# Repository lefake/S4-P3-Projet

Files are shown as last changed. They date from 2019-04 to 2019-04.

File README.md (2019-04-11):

# S4-P3-Projet
PCB maker project



This is a PCB maker device, it is use to create PCB from an image in black and white. Three software are include in this repo : 
  - GCode Generator :
      Create a GCode file form an image of the PCB
  - Device communication :
      Send a GCode file to the device
      Manual control of the device
  - GCode Interpreter :
      Move motors from a GCode command

For more documentation on each software read the README files in every directory.

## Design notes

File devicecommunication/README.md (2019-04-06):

# Device Communication

This code is use to communicate with the device

## Getting Started

To use this UI you must have a GCode file to sent to the device unless you want to control manually the device.

### Prerequisites

Since the program is coded in python, you need to install python, we used python 3.7.
You can use an IDE or cmd to launch the program or the UI.

## Using the program

After downloading the project,
You can launch CommunicationMain.py in S4-P3-Projet/devicecommunication/ for the user interface of the program.

### Automatic mode

Enter the parameters in the proper boxes:

```
- The GCode file's path.
- COM port of the OpenCR (ex: COM8).
- The communication baudrate of the OpenCR.
- Maximum communication time in seconds.
  This is the maximum time to accept an anwser when a command is request.
- Sleep inital time in seconds. 
  This is the boot time of the OpenCR. The time to wait before sending the first command.
```
Once all parameters are entered, you can click on the **Start** button.
At the moment everything runs in one thread so the UI is block by the communication

### Manual mode

The manual mode uses the values entered in the Auto tab so be sure the COM port is specified.
At the moment all +/- buttons dont move the motors in a relative movement. 
Hence it's better to use the text field to move the mototrs

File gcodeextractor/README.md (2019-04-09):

# GCode Extractor

This program transforms a pcb drawing into a gcode.

## Getting started

To use this program, you need to launch main.py with the proper parameters or launch UI.py in /UI/ and enter the parameters in the boxes.
The PCB drawing you are using needs to be of format *.pbm ,
there are plenty of converters online to change your file format, such as [this converter we used](https://convertio.co/fr/pdf-pbm/).

### Prerequisites

Since the program is coded in python, you need to install python, we used python 3.7.
You can use an IDE or cmd to launch the program or the UI.

### Using the program

After downloading the project, you can launch UI.py in S4-P3-Projet/gcodeextractor/UI/ for the user interface of the program.

Enter the parameters in the proper boxes:

```
- Pcb drawing file path you want to convert into gcode, this file needs to be of type *.pbm
- Gcode file you want to save with the path where you want to save it.
  If the file doesn't exist, a new file will be created, file type needs to be *.gcode
- If the pbm file is of type binary or ASCII. To find the type, you can open the file in a text editor,
  ASCII files will start with P1 while binary with P4. Also, binary type will contain unreadable characters.
- Width of your pcb, units are entered later, 
- Height of your pcb, it must be of the same units as the width
- Radius of the tool you are using, units must be in mm.
- Units type for the width and height
```
Once all parameters are entered, you can click on the **execute program** button.
If everything is good, you should read **SUCCESS** on the bottom of the UI, else and error code should appear.

### Algorithms

To convert a pcb image into a gcode, we first find where the tool will have to travel, in order to create the pcb. This is done in the path.py file. The pcb image is a matrix in which the connections are represented by 1's and the empty space by 0's, we use 2's to represent the tool's path. path.py has 3 functions, the first one (scanHorizontal) adds 2's on the left or the right of 1's if they are the beginning or end of a line, it adds a column of 2's the size of the tool's diameter at a tool's radius away from the 1. the second function (scanVertical) is similar but instead of looking and adding on the left or right side, it does on the up or down side. The third function (twoRemoving) removes 2's where there shouldn't be, by looking near the 1's and removing 2's that would make the tool touch the 1.

We then create a sequence of coordinates for the tool to follow to cover all the path we just created. This is done in gcodeCreator.py. We create a sequence of straight lines only, circles or diagonals are a sum of straight lines. The sequence is created by the function *create sequence* that goes through all pixels in the image to find a 2 where the tool will start working. It starts the sequence by a set of coordinates (-1,-1), which means it is starting a new path, and a set of coordinates where the 2 is. Then it uses the function *findDirection* to seek for 2's nearby to find a direction where to travel. It will continue in this direction with the function *findEndOfLine* until it hits the last 2 of the line, adding its coordinates to the sequence, and then seek for another direction until it can't find any 2's. All the 2's covered by the sequence are changed by 3's so the algorithm never cover the same 2 twice. Once it comes to the end of a path, the algorithm will continue looking for 2's where to start paths from until it has looked through all the pixels of the image.

The last file is GcodeBuilder.py, it transforms the sequence of point into a standard gcode file. It does so by changing the coordinates in pixels, into coordinates in mm according to the dimensions of the pcb. If the coordinates are (-1,-1), this means the sequence has finished a path and the tool should not be working until it gets to the next coordinates. The gcode file also starts with a header and ends with a footer to add some configurations and a homing.

### Tests

For path.py's function, we tested the three functions with small matrix of 0's and 1's and wrote the expected results manually to compare if the functions returned what we expected. We also tested if the algorithms would still work if it had to write or read out of bound of the image, which is verified in the algorithms. 

The tests for GcodeCreator.py were made in a similar way, with small matrices of 0's and 2's and an expected sequence of coordinates to compare. We also tested if the algorithm had to read out of bound of the image.

For GcodeBuilder.py, we created some coordinates sequences and a similar but simpler algorithm that would give us the resulting gcode. We compared the function's results with the simpler algorithm's results to see if they were the same. We also tested for different pixel sizes.

## Authors

**Ian Lalonde** 

**Marc-Antoine Lafrenière**

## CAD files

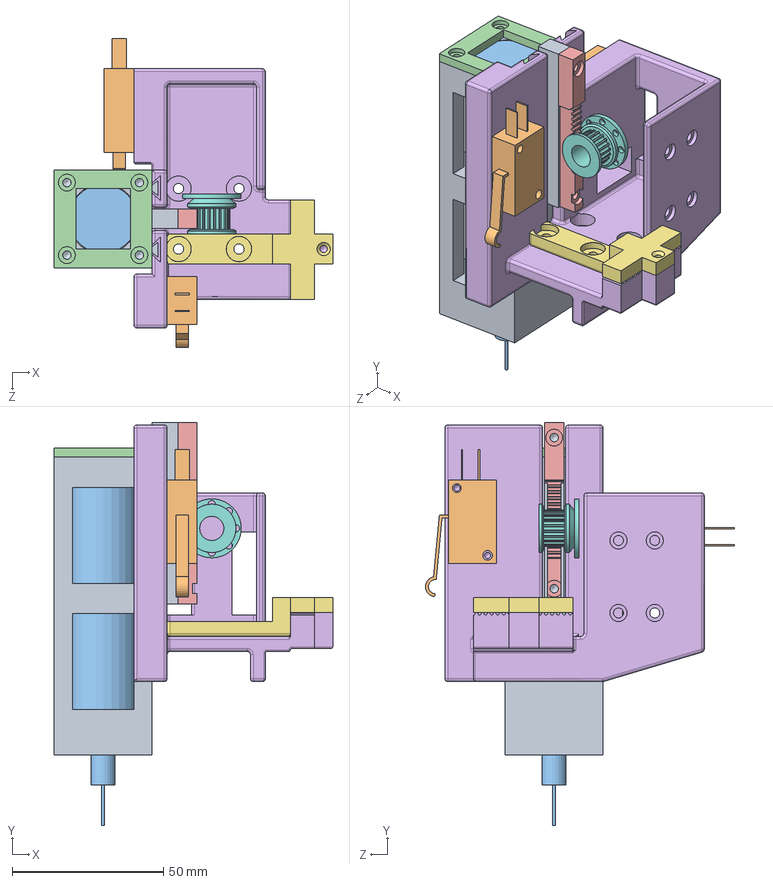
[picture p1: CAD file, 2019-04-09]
Machine PCB/assemblage dremel.SLDASM
92.2 x 133.4 x 102.3 mm
support dremel male
LIMIT SWITCH x 2
modèle dremel
couvercle support
gear
support dremel
Adapteur_MGN14
GT2_20T_Costom2

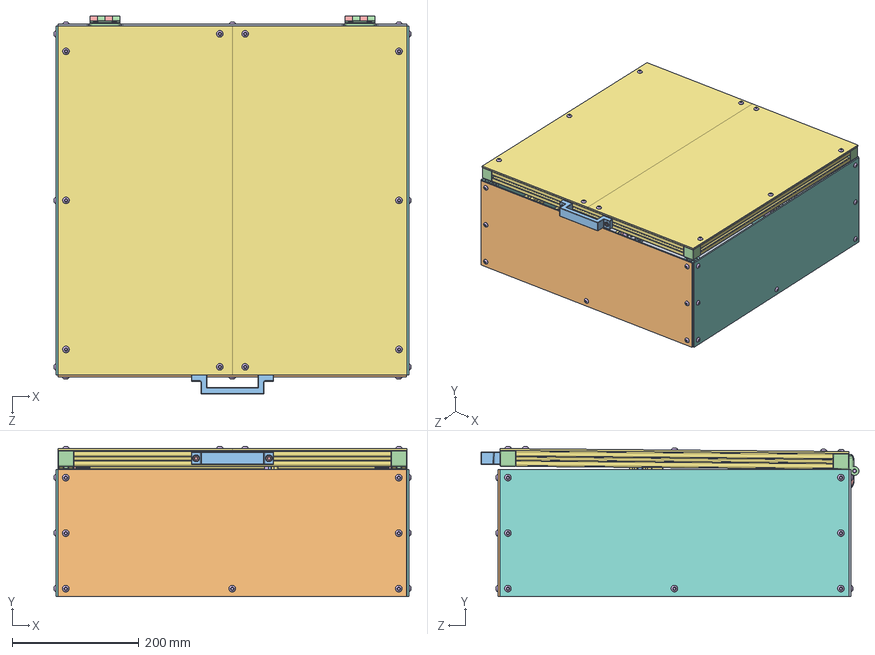
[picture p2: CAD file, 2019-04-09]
Machine PCB/Assemblage.SLDASM
562.6 x 236.6 x 595.9 mm
MGN_12_H_RAIL x 2
MGN_12_H_CARRAGE x 3
MGN_12_H_RAIL_310mm
Adapteur_MGN12 x 2
socket head cap screw_am x 61
94180A351_HEAT-SET INSERTS FOR PLASTICS x 2
25_2525_500mm x 15
14164_m x 22
Adapteur_MGN12_2
Adapteur_MGN12_3
Support_moteur_axe_y_1
634068.step x 3
545412.step x 6
535198.step x 6
socket head cap screw_ai x 12
GT2_20T_Costom
GT2_20T x 3
Adapteur_support_bearing
633104.step x 4
coupleur
Plaque_bearing
Belt_1
Belt_2
Panneau_1 x 2
Panneau_3
Panneau_2
handle
_12099_m_a_2 x 2
_12099_m_b_4 x 2
_12098_m_pin_6 x 2
socket countersunk head screw_am x 8
25_2525_200mm x 4
bed_2
bed_1
moteurgros x 2
coins_couvercle x 4
fer_angle x 5
socket button head cap screw_am x 60
Panneau_4 x 2
X-430_IDLE.stp
X-430_SPACER_RING.stp x 8
X-430_CVR_CABLE.stp
bed corner
bed slider x 2
braquette_1_LS
LIMIT SWITCH x 5
braquette_2_LS
Panneau_5
Panneau_6
braquette_3_LS
support dremel male
modèle dremel
couvercle support
gear
support dremel
Adapteur_MGN14
GT2_20T_Costom2
flat head screw_am
hex screw_am x 3

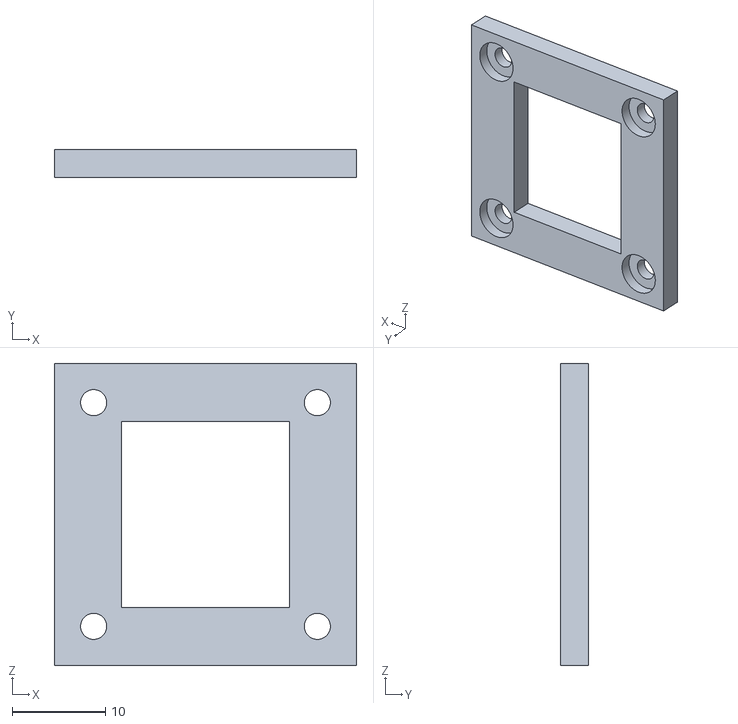
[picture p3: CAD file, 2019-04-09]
Fichiers STL/couvercle support.STL
32.4 x 3.00 x 32.4

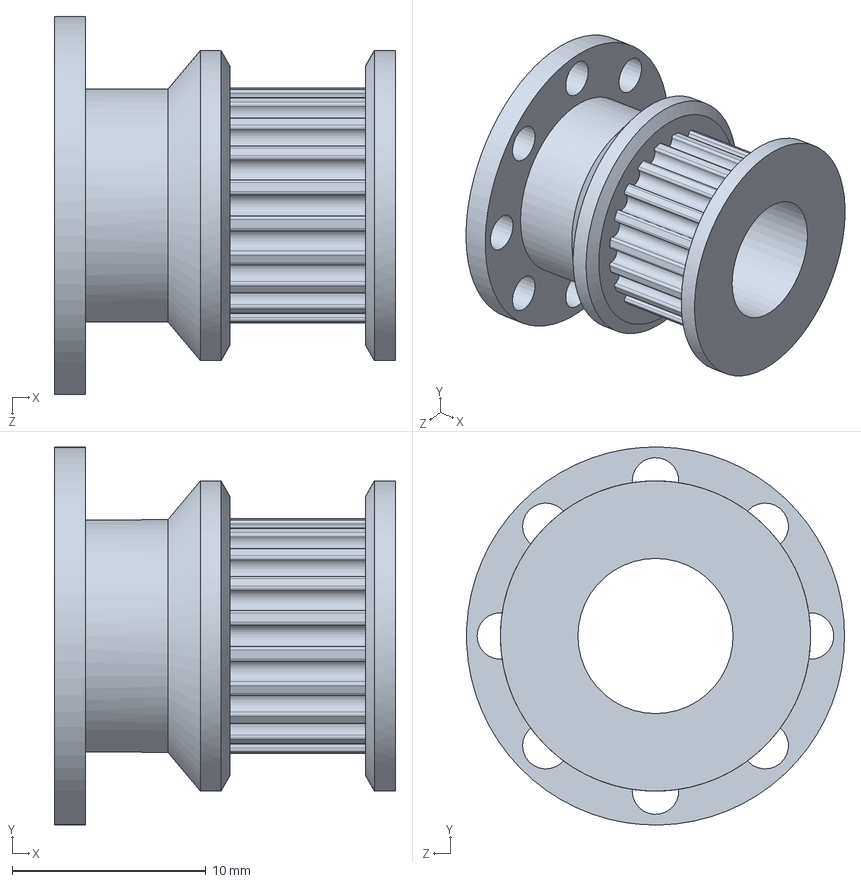
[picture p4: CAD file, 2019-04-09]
Machine PCB/GT2_20T_Costom.SLDPRT
17.6 x 19.5 x 19.5 mm

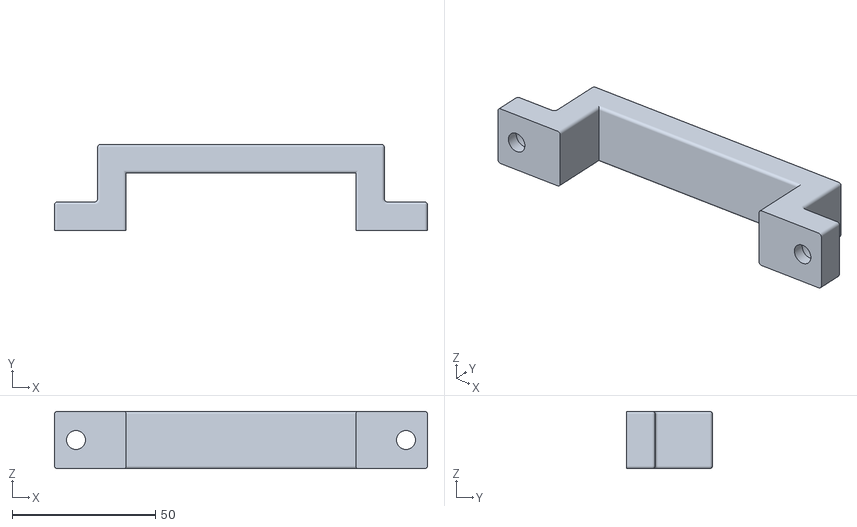
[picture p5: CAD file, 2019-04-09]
Fichiers STL/handle.STL
130.0 x 30.0 x 20.0

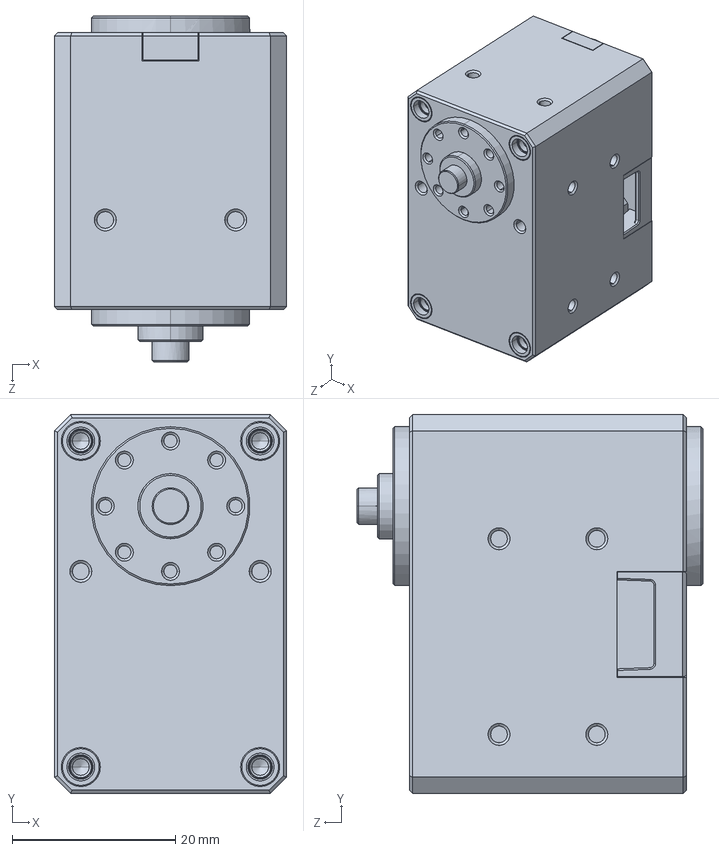
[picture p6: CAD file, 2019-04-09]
Machine PCB/moteurgros.SLDPRT
28.5 x 46.5 x 42.4 mm

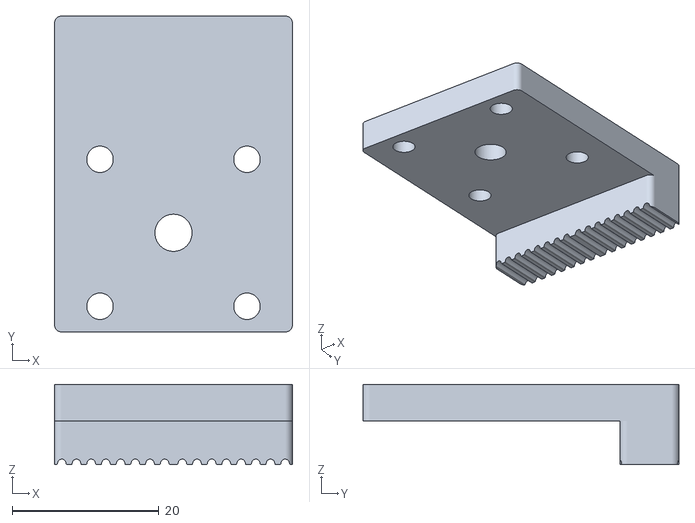
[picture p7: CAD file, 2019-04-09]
Fichiers STL/Adapteur_MGN12.STL
32.4 x 43.0 x 10.9

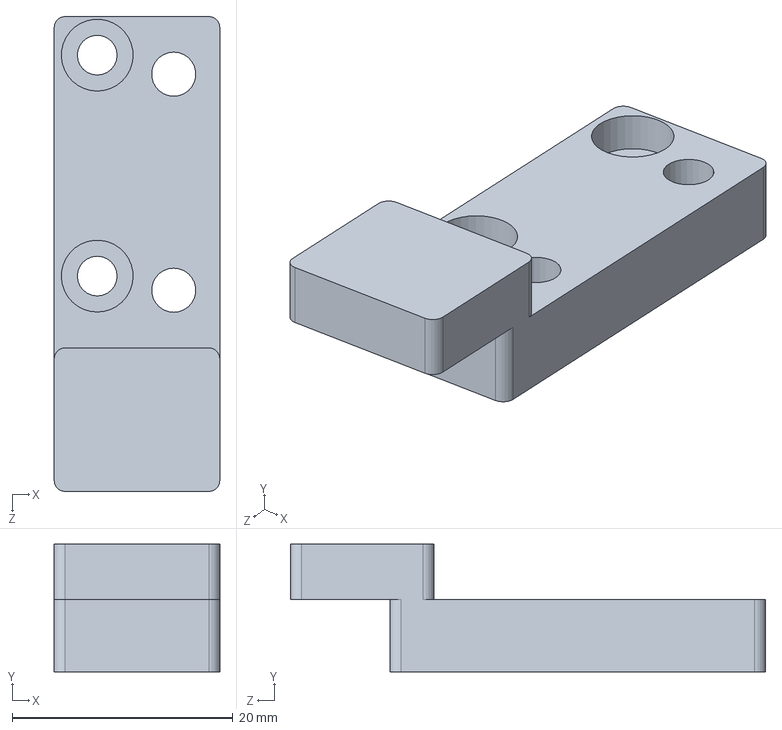
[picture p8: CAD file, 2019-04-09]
Machine PCB/Adapteur_MGN12_2.SLDPRT
15.0 x 11.6 x 43.0 mm

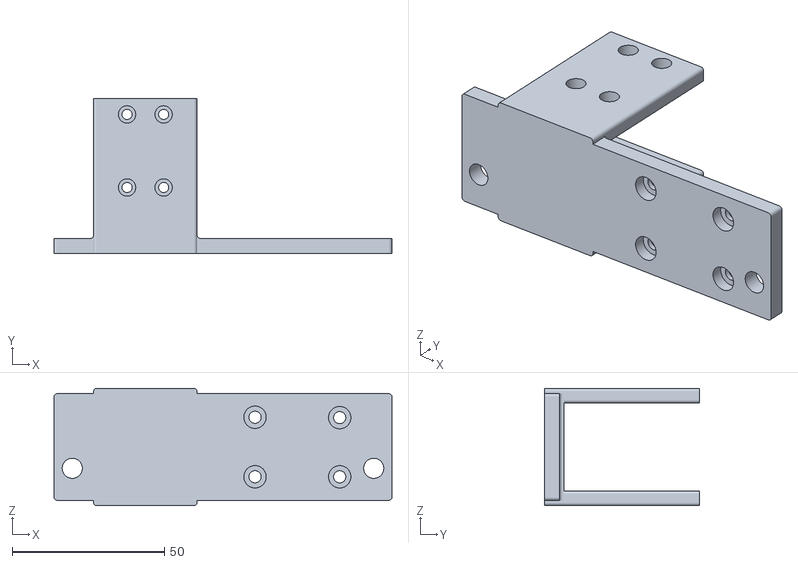
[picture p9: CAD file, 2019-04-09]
Fichiers STL/Adapteur_support_bearing.STL
111.0 x 50.9 x 38.5

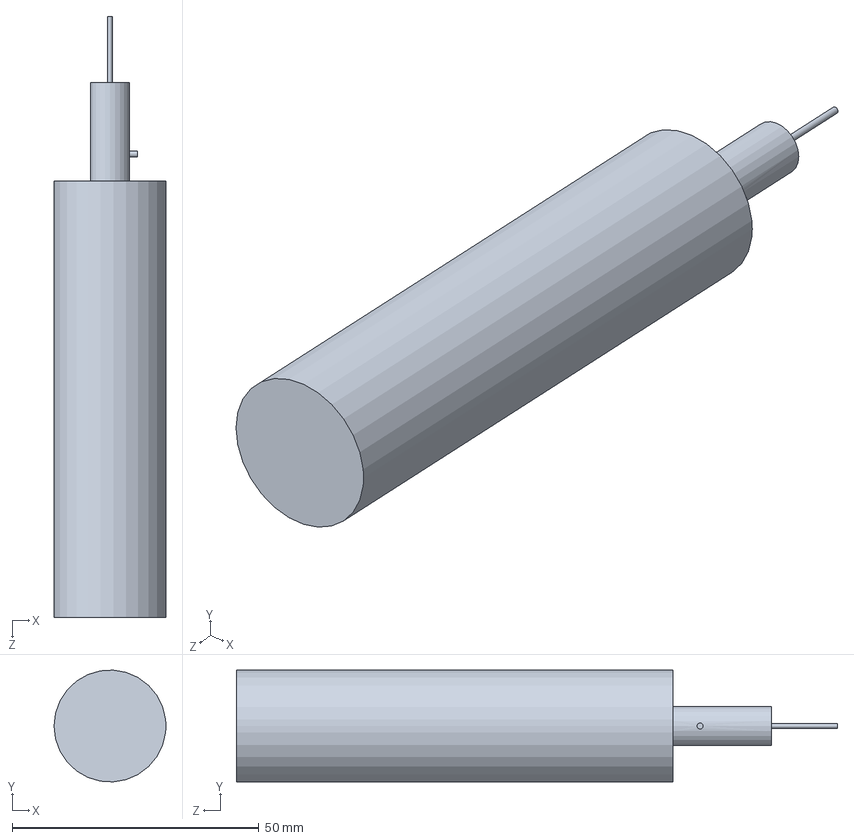
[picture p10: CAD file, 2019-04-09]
Machine PCB/modèle dremel.SLDPRT
22.7 x 22.7 x 121.9 mm

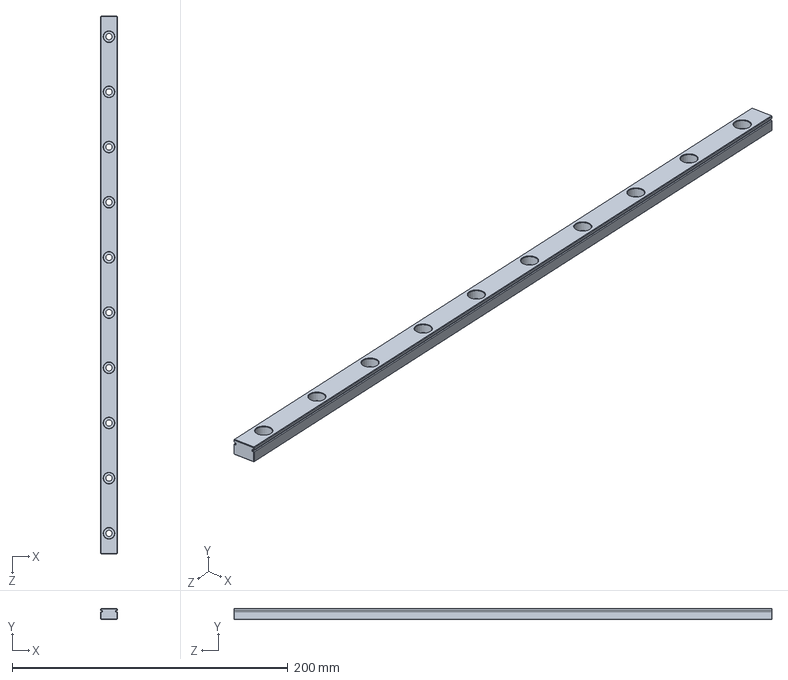
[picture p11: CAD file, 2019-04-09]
Machine PCB/MGN_12_H_RAIL.SLDPRT
12.0 x 8.00 x 390.0 mm

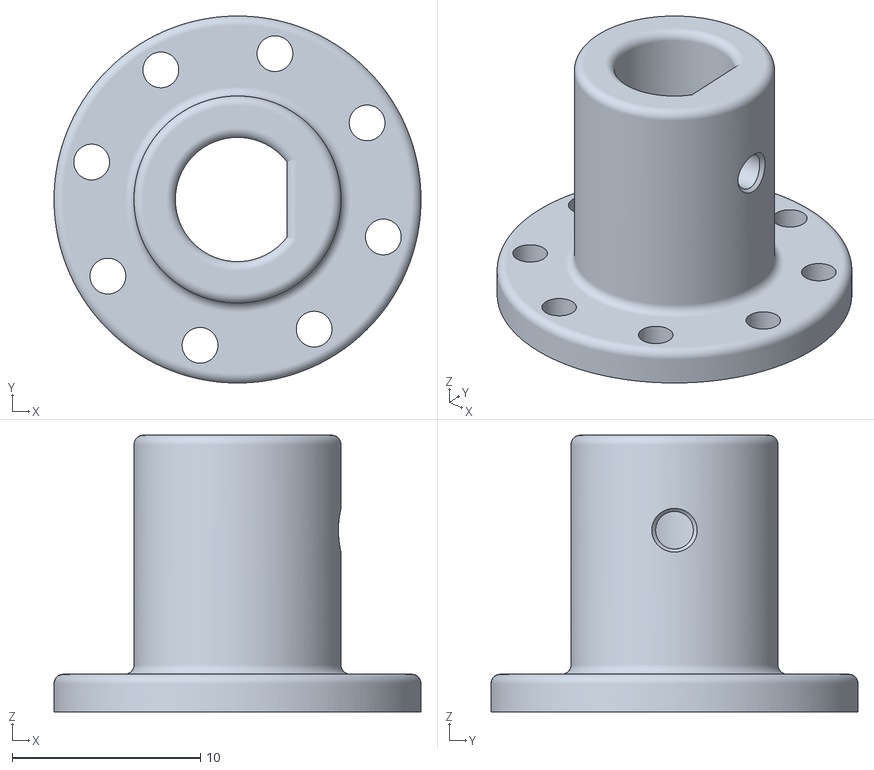
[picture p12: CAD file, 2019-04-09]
Fichiers STL/coupleur.STL
19.5 x 19.5 x 14.7

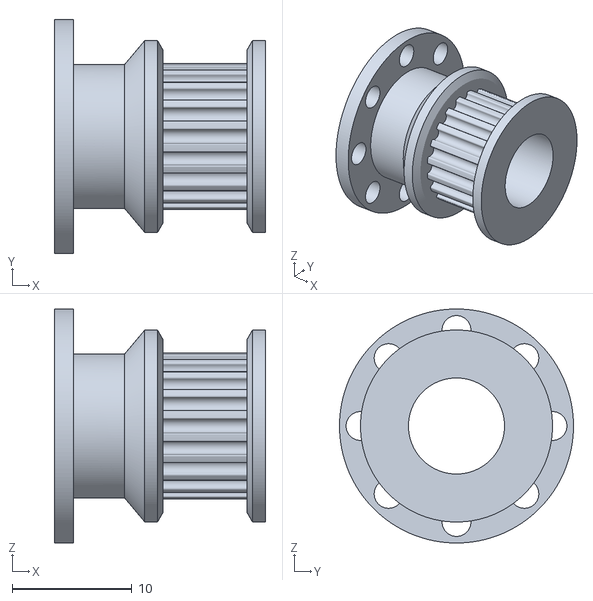
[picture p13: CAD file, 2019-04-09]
Fichiers STL/GT2_20T_Costom.STL
17.6 x 19.5 x 19.5

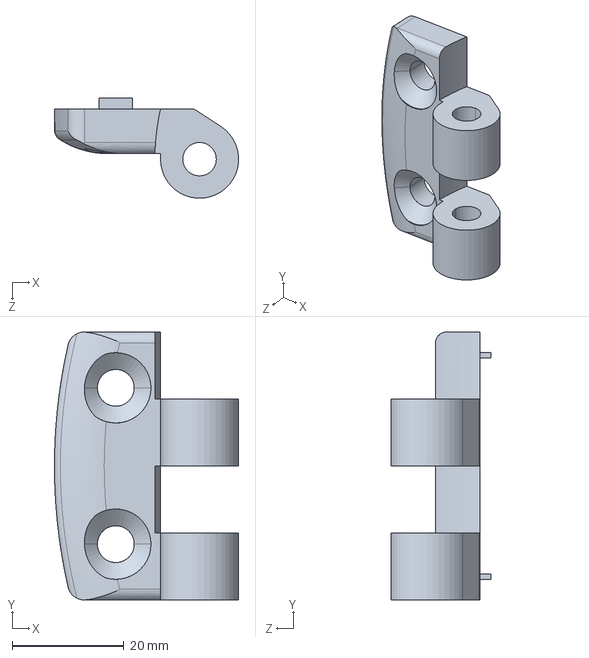
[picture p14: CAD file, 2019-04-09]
Machine PCB/_12099_m_a_2.sldprt
33.0 x 48.0 x 18.0 mm

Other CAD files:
Fichiers STL/Adapteur_MGN12_3.STL
Fichiers STL/Plaque_bearing.STL
Machine PCB/braquette_1_LS.SLDPRT
Fichiers STL/braquette_3_LS.STL
Fichiers STL/Adapteur_MGN12_2.STL
Fichiers STL/Support_moteur_axe_y_1.STL
Fichiers STL/T_NUT_M3.STL
Fichiers STL/braquette_1_LS.STL
Fichiers STL/braquette_2_LS.STL
Fichiers STL/coins_couvercle.STL
Fichiers STL/gearRack.STL
Fichiers STL/support dremel male.STL
Machine PCB/14164_m.sldprt
Machine PCB/25_2525_200mm.SLDPRT
Machine PCB/25_2525_500mm.SLDPRT
Machine PCB/535198.STEP
Machine PCB/545412.STEP
Machine PCB/633104.STEP
Machine PCB/634068.STEP
Machine PCB/94180A351_HEAT-SET INSERTS FOR PLASTICS.SLDPRT
Machine PCB/Adapteur_MGN12.SLDPRT
Machine PCB/Adapteur_MGN12_3.SLDPRT
Machine PCB/Adapteur_MGN14.SLDPRT
Machine PCB/Adapteur_support_bearing.SLDPRT
Machine PCB/Belt_1.SLDPRT
Machine PCB/Belt_2.SLDPRT
Machine PCB/GT2_20T.SLDPRT
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

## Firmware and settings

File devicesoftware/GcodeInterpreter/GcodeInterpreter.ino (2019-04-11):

/*******************************************************************************
Title : OpenCR
Date : April 10th 2019
Authors : Maxime Desmarais-Laporte and Marc-Antoine Lafreniere

Descritpion : 
  GCode interpretor, use in a PCB maker device.

  The device has 3 limits switches (one for every axis) use for a homing of the device
  These switches are attach to one interrupt and to 3 digital pins.
  The interrupt was noizy so a filter is apply to the interrupt


Interrupt filter :
  To filter the noize on the interrupt we use the digital pin connected to the NC of the switch
  The filter simply looks if the digital pin is LOW for *debounceTimeFalling* time
  If it stays LOW for the whole *debounceTimeFalling* then a flag is set to true
  If it stays HIGH for the whole *debounceTimeRising* then a flag is set to false

GCode status :
  G0 Xx Yy Zz       Done
  G28               Done
  G90               Inactive
  G91               Not implemeted
  M18               Done
  M112              Done

Commincations :
  When a command is recived, "2" is printed to the Serial port
  When the command is done executing, "1" is printed to the Serial port

  If the command can't complete, "-1" is printed to the Serial port
  If the device is in eStop mode, "-2" is printed to the Serial port on a commmand request


Electrical :
  The 3 homing switches are connected the same way :
    NC to a digital pin
    NO to the interrupt
    COM to the ground
  Hence every digital and interrupt pin MUST be in INPUT_PULLUP


TODO :
  Connect 2 switches on the other end of the X and Y axis as a fail-safe and add a filter if needed
  Change some variable usage : at the moment everything works only if motors' ids are +1 between each (ex: x=9, y=10, z=11)

Specifications :
  Baud for motors : 57600 b/s

Dynamixel and OpenCR documentation :
  http://emanual.robotis.com/docs/en/dxl/x/xm430-w350/
  http://emanual.robotis.com/docs/en/parts/controller/opencr10/
*******************************************************************************/
#include <DynamixelWorkbench.h>
#include "functions.h"
#include "models.h"

#if defined(__OPENCM904__)
  #define DEVICE_NAME "3"
#elif defined(__OPENCR__)
  #define DEVICE_NAME ""
#endif

#define STRING_BUF_NUM 64
#define MINTICK 0
#define MAXTICK 1048575
const int ACCEPTABLE_RANGE[3] = { 2, 2, 4 };

const String HOMING_OFFSET = "Homing_Offset";
const String OPERATING_MODE = "Operating_Mode";
const String PRESENT_POSITION = "Present_Position";
const String GOAL_POSITION = "Goal_Position";

// 0 = not reverse, 1 = reverse
uint8_t X_REVERSE = 0;
uint8_t Y_REVERSE = 1;
uint8_t Z_REVERSE = 0;

// Dynamixel variables
DynamixelWorkbench dxl_wb;
String cmd[STRING_BUF_NUM];
uint8_t get_id[16];
uint8_t scan_cnt = 0;
uint8_t ping_cnt = 0;
const char *NULL_POINTER = NULL;

// Motors Propertys :
uint8_t idX = 11;
uint8_t idY = 12;
uint8_t idZ = 13;

// Mecanicals propertys:
const float pouleyPitch = 2;  //mm
const int nbTheets = 20;
const int resMotorTick = 4096;  //Ticks per revolution

int32_t tickFromMm = resMotorTick/(pouleyPitch*nbTheets);

// Limit Switch propertys
const int xSwitchPin = 8;
const int ySwitchPin = 9;
const int zSwitchPin = 10;
const int emergencySwitchPin = 2; // intrupt pin

// Homing variables
bool homing = false;
bool homingX = false;
bool homingY = false;
bool homingZ = false;
int homingState = 0;

const int homeOffsetX = 28*tickFromMm;
const int homeOffsetY = 19.5*tickFromMm;
const int homeOffsetZ = 2.5*tickFromMm;

// Debounce timer variables
bool isFalling = false;
long debounceTimeFalling = 250;
long lastTimeXFalling = 0;
long lastTimeYFalling = 0;
long lastTimeZFalling = 0;

bool isRising = false;
long debounceTimeRising = 250;
long lastTimeXRising = 0;
long lastTimeYRising = 0;
long lastTimeZRising = 0;

bool isXSwitchPress = false;
bool isYSwitchPress = false;
bool isZSwitchPress = false;

// eStop
bool isEmegencyState = false;
bool ledX = false;
bool ledY = false;
bool ledZ = false;

// Moving variables
bool isMoving = false;
bool currentMoveDone = false;
bool hasFailed = false;
int currentMove = 0;
int nbsMovements = 0;
int32_t currentPosition = 0;
int32_t movingSpeed[] = { 75, 75 };
MovingCommand commands[3];

void setup() 
{
  // Initialisation des pins :
  pinMode(xSwitchPin, INPUT_PULLUP);
  pinMode(ySwitchPin, INPUT_PULLUP);
  pinMode(zSwitchPin, INPUT_PULLUP);
  pinMode(emergencySwitchPin, INPUT_PULLUP);
  attachInterrupt(digitalPinToInterrupt(emergencySwitchPin), LimiteSwitch, CHANGE);
  
  Serial.begin(57600);

  //Motor Initialisation Section :
  Begin((uint32_t)57600);
  Ping(idX);
  Ping(idY);
  Ping(idZ);
  Scan();
  
  delay(1000);
  
  Torque_off(idX);
  Torque_off(idY);
  Torque_off(idZ);
  
  Write(idX, 4, OPERATING_MODE);
  Write(idY, 4, OPERATING_MODE);
  Write(idZ, 4, OPERATING_MODE);

  Write(idX, 0, HOMING_OFFSET);
  Write(idY, 0, HOMING_OFFSET);
  Write(idZ, 0, HOMING_OFFSET);

  dxl_wb.writeRegister(idX, 10, 1, &X_REVERSE, &NULL_POINTER);
  dxl_wb.writeRegister(idY, 10, 1, &Y_REVERSE, &NULL_POINTER);
  dxl_wb.writeRegister(idZ, 10, 1, &Z_REVERSE, &NULL_POINTER);

  Write(idX, movingSpeed[0], "Profile_Velocity");
  Write(idY, movingSpeed[1], "Profile_Velocity");

  Torque_on(idX);
  Torque_on(idY);
  Torque_on(idZ);

  resetMovingVariables();
}

void loop() 
{
  if(isFalling)
  {
    if(digitalRead(xSwitchPin))
    {
      if(millis() - lastTimeXFalling > debounceTimeFalling)
      {
        lastTimeXFalling = millis();
        isFalling = false;
        isXSwitchPress = true;

        // Insert what to do if the button is press (executed on change)
        if(homingX)
        {
          homingX = false;
          OffsetAxe(idX, homeOffsetX);
          Torque_off(idX);
          Write(idX, 4, OPERATING_MODE);
          Torque_on(idX);
          
          currentMove = 0;
          nbsMovements = 1;
          commands[currentMove]._motorId = idX;
          commands[currentMove]._goalPosition = 0;
          isMoving = true;
          Write(commands[currentMove]._motorId, commands[currentMove]._goalPosition, GOAL_POSITION); 
        }
        else
        {
          isEmegencyState = true;
          ledX = true;
        }
      }
    }
    else
    {
      lastTimeXFalling = millis();
      isXSwitchPress = false;
    }

    if(digitalRead(ySwitchPin))
    {
      if(millis() - lastTimeYFalling > debounceTimeFalling)
      {
        lastTimeYFalling = millis();
        isFalling = false;
        isYSwitchPress = true;

        // Insert what to do if the button is press (executed on change)
        if(homingY)
        {
          homingY = false;
          OffsetAxe(idY, homeOffsetY);
          Torque_off(idY);
          Write(idY, 4, OPERATING_MODE);
          Torque_on(idY);
          
          currentMove = 0;
          nbsMovements = 1;
          commands[currentMove]._motorId = idY;
          commands[currentMove]._goalPosition = 0;
          isMoving = true;
          Write(commands[currentMove]._motorId, commands[currentMove]._goalPosition, GOAL_POSITION);
        }
        else
        {
          isEmegencyState = true;
          ledY = true;
        }
      }
    }
    else
    {
      lastTimeYFalling = millis();
      isYSwitchPress = false;
    }

    if(digitalRead(zSwitchPin))
    {
      if(millis() - lastTimeZFalling > debounceTimeFalling)
      {
        lastTimeZFalling = millis();
        isFalling = false;
        isZSwitchPress = true;
        
        // Insert what to do if the button is press (executed on change)
        if(homingZ)
        {
          homingZ = false;
          OffsetAxe(idZ, homeOffsetZ);
          Torque_off(idZ);
          Write(idZ, 4, OPERATING_MODE);
          Torque_on(idZ);

          currentMove = 0;
          nbsMovements = 1;
          commands[currentMove]._motorId = idZ;
          commands[currentMove]._goalPosition = 0;
          isMoving = true;          
          Write(commands[currentMove]._motorId, commands[currentMove]._goalPosition, GOAL_POSITION);
        }
        else
          {
          isEmegencyState = true;
          ledZ = true;
        }
      }
    }
    else
    {
      lastTimeZFalling = millis();
      isZSwitchPress = false;
    }

    if(!digitalRead(xSwitchPin) && !digitalRead(ySwitchPin) && !digitalRead(zSwitchPin))
      isFalling = false;
  }

  if(isRising)
  {
    if(!digitalRead(xSwitchPin))
    {
      if(millis() - lastTimeXRising > debounceTimeRising)
      {
        lastTimeXRising = millis();
        isRising = false;
        isXSwitchPress = false;
        // Insert what to do if the button is release (executed on change)
      }
    }
    else
      lastTimeXRising = millis();

    if(!digitalRead(ySwitchPin))
    {
      if(millis() - lastTimeYRising > debounceTimeRising)
      {
        lastTimeYRising = millis();
        isRising = false;
        isYSwitchPress = false;
        // Insert what to do if the button is release (executed on change)
      }
    }
    else
      lastTimeYRising = millis();

    if(!digitalRead(zSwitchPin))
    {
      if(millis() - lastTimeZRising > debounceTimeRising)
      {
        lastTimeZRising = millis();
        isRising = false;
        isZSwitchPress = false;
        // Insert what to do if the button is release (executed on change)
      }
    }
    else
      lastTimeZRising = millis();

    if(digitalRead(xSwitchPin) && digitalRead(ySwitchPin) && digitalRead(zSwitchPin))
    {
      isRising = false;
    }
  }

  if(isMoving)
  {
    currentPosition = Read(commands[currentMove]._motorId, PRESENT_POSITION);
    if(isInRange(currentPosition, commands[currentMove]._goalPosition, commands[currentMove]._motorId))
    {
      currentMoveDone = true;
    }
  }

  if(isMoving && currentMoveDone)
  {
    if(currentMove+1 >= nbsMovements)
    {
      if(homing)
      {
        if(commands[currentMove]._motorId == idZ)
        {
          homingY = true;
          HomingAxis(idY, -100);
          homingState++;
        }
        else if(commands[currentMove]._motorId == idY)
        {
          homingX = true;
          HomingAxis(idX, -100);
          homingState++;
        }
        else if(commands[currentMove]._motorId == idX)
        {
          homingState++;
          homing = false;
          Serial.println(homingState == 3 ? "1" : "-1");
          homingState = 0;

          Write(idX, movingSpeed[0], "Profile_Velocity");
          Write(idY, movingSpeed[1], "Profile_Velocity");
        }
        resetMovingVariables();
      }
      else
      {
        resetMovingVariables();
        Serial.println("1");
      }
    }
    else
    {
      currentMoveDone = false;
      currentMove++;
      Write(commands[currentMove]._motorId, commands[currentMove]._goalPosition, GOAL_POSITION);
    }
  }
  
  if(isEmegencyState)
    setEmergency();
  
  if (!homing && !isMoving && Serial.available())
  {
    String read_string = Serial.readStringUntil('\n');
    if(!isEmegencyState)
    {
      String words[] = {"", "", ""};
      
      int start = 0;
      int wordIndex = 0;
      int statut[3] = {0, 0, 0};
      
      for(int i = 1; i < read_string.length(); i++)
      {
        if(read_string.charAt(i) == ' ')
        {
          words[wordIndex++] = read_string.substring(start, i);
          start = i+1;
        }
      }
      words[wordIndex] = read_string.substring(start, read_string.length());
      nbsMovements = wordIndex;
      Serial.println("2");

      if(words[0] == "G0")
      {
        int i;
        for(i = 1; i < wordIndex+1; i++)
        {
            if(words[i].length() > 1)
            {
                float value = words[i].substring(1, words[i].length()).toFloat();
                uint8_t idMotor = getIdFromChar((char)words[i].charAt(0));
                if(idMotor == -1)
                {
                  Serial.println("-1");
                  break;
                }
                else
                {
                  commands[i-1]._motorId = idMotor;
                  commands[i-1]._goalPosition = value*tickFromMm;
                }
            }
            else
            {
              Serial.println("-1");
              break;
            }
        }
        
        if(i == wordIndex+1)
        {
          isMoving = true;
          currentMove = 0;
          Write(commands[currentMove]._motorId, commands[currentMove]._goalPosition, GOAL_POSITION);
        }
      }
      
      else if(words[0] == "G28")
      {
        homing = true;
        homingZ = true;
        HomingAxis(idZ, -50);
      }
      else if(words[0] == "M18"){
          TorqueOffAll();
          Serial.println("1");
      }
      else if(words[0] == "M112"){
          setEmergency();

          Led(idX, 1);
          Led(idY, 1);
          Led(idZ, 1);

          Serial.println("1");
      }
      else if(words[0] == "G90")
      {
        Serial.println("1");
      }
      else
      { 
        Serial.println("-1");
      }
    }
    else
    {
      Serial.println("-2");
    }
  }
}

uint8_t getIdFromChar(char letter)
{
    if(letter == 'X')
        return idX;
    else if(letter == 'Y')
        return idY;
    else if(letter == 'Z')
        return idZ;
    else
        return -1;
}

bool isInRange(int goal, int curPos, uint8_t id)
{
  return (abs(goal - curPos) <= ACCEPTABLE_RANGE[id-idX]);
}

void resetMovingVariables()
{
  isMoving = false;
  currentMoveDone = false;
  currentMove = 0;
  nbsMovements = 0;
  currentPosition = 0;
  hasFailed = false;

  for(int i = 0; i < 3; i++)
  {
    commands[i]._motorId = i+idX;
    commands[i]._goalPosition = Read(i+idX, PRESENT_POSITION);
  }
}

void HomingAxis(uint8_t id, int speed)
{
  Torque_off(id);
  Write(id, 0, HOMING_OFFSET);
  Torque_on(id);
  Wheel(id, speed);
}

void OffsetAxe(uint8_t id, int offset){
  int32_t posPresent = Read(id, PRESENT_POSITION);
  int32_t homePosition = - posPresent - offset;
  Torque_off(id);

  if(id == idX && X_REVERSE)
    homePosition *= -1;
  else if(id == idY && Y_REVERSE)
    homePosition *= -1;
  else if(id == idZ && Z_REVERSE)
    homePosition *= -1;
  
  Write(id, homePosition, HOMING_OFFSET);
  Torque_on(id);
}

void LimiteSwitch(){
  if(!digitalRead(emergencySwitchPin))
    isRising = true;
  else
    isFalling = true;
}

void setEmergency()
{
  isMoving = false;
  TorqueOffAll();
  Led(idX, ledX);
  Led(idY, ledY); 
  Led(idZ, ledZ);
}

void changeMode(uint8_t id)
{
  Write(id, 4, OPERATING_MODE);
}


//########################
// Low Levels functions :
//########################

void Begin(uint32_t baud){
  if (cmd[1] == '\0')
  cmd[1] = String("57600");
  
  dxl_wb.init(DEVICE_NAME, baud);
}

void Ping(int identification){
  get_id[ping_cnt] = identification;
  uint16_t model_number = 0;
  dxl_wb.ping(get_id[ping_cnt], &model_number, &NULL_POINTER); 
}

void Scan(){
  uint8_t range = 253;
  dxl_wb.scan(get_id, &scan_cnt, range);  
}

void Joint(uint8_t id, int32_t goal){
  dxl_wb.jointMode(id, 0, 0, &NULL_POINTER);
  dxl_wb.goalPosition(id, goal, &NULL_POINTER);
}

void Wheel(uint8_t id, int32_t goal){
  dxl_wb.wheelMode(id, 0, &NULL_POINTER);
  dxl_wb.goalVelocity(id, goal, &NULL_POINTER);
}

void Torque_on(uint8_t id){
  dxl_wb.torqueOn(id, &NULL_POINTER);
}

void Torque_off(uint8_t id){
  dxl_wb.torqueOff(id, &NULL_POINTER);
}

void Write(uint8_t id, uint32_t value, String commande){
  dxl_wb.writeRegister(id, commande.c_str(), value, &NULL_POINTER);
}

int32_t Read(uint8_t id, String commande){
  int32_t data = 0;
  dxl_wb.readRegister(id, commande.c_str(), &data, &NULL_POINTER);
  return data;
}

void Led(uint8_t id, bool state){
  Write(id, (uint32_t)state, "LED");
}

void TorqueOffAll(){
      Torque_off(idX);
      Torque_off(idY);
      Torque_off(idZ);
}

void TorqueOnAll(){
      Torque_on(idX);
      Torque_on(idY);
      Torque_on(idZ);
}

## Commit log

2019-01-23 #19 - Reformat pbm file
    Convert pbm file to csv with right height and width
    [test1.csv]
2019-02-04 #16 create test bench
    6 first test images
    [testvert.csv]
2019-02-05 #24 Create project structure for unit tests
    Refactor project's structure
    closes #24
    [test1.csv, testvert.csv]
2019-02-12 File utils refactor and unittests
    Create unit test for file utils
    closes #25
    closes #26
    [test1.csv]
2019-02-27 Send all GCode command
    Read a gcode file and send it to the arduino
2019-03-18 #42 Run the c++ code to convert PBM binary to ascii
    Run the converter if the image is in binary
    [test100x100.csv]
2019-03-20 #56-Delay in Arduino communication
    Wait for input from the arduino before sending next GCode command
2019-03-20 #55-UI frame
    Refactor main the ease usage in the UI
2019-03-26 Building of G-28 request
    This commit is for the implementation of the request G28, M18 and M112. G28 is for Homing, M18 is for emergency stop and M112 is for a full stop.
2019-03-27 #60 Create UI to control the device
    Create a UI to control the device in manual mode and auto mode
2019-04-06 Refactor and bug fixes
    Fix homing issue
    Add motor direction as constant
    [GcodeInterpreter.ino]
2019-04-06 Bug fixes
    Fix emergency state issue
    [GcodeInterpreter.ino]
2019-04-06 Rename modules
    Rename modules with better name and move the arduino code to its own folder
    [test1.csv, test100x100.csv, testvert.csv]
2019-04-07 Homing issues
    Fix homing if axis is reverse
    [GcodeInterpreter.ino]
2019-04-07 Noise filter
    Add noise filter to all limit switches
    [GcodeInterpreter.ino]
2019-04-08 All stl files
    [Adapteur_MGN12.STL, Adapteur_MGN12_2.STL, Adapteur_MGN12_3.STL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]
2019-04-08 Solidworks complete assembly
    [14164_m.sldprt, 25_2525_200mm.SLDPRT, 25_2525_500mm.SLDPRT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]
2019-04-08 Remove unused files
    [25_2525_240mm.SLDPRT, 25_2525_480mm.SLDPRT, Adapteur_MGN12.SLDPRT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]
2019-04-10 Fixing bugs
    Removed blocking whiles
    [GcodeInterpreter.ino]
